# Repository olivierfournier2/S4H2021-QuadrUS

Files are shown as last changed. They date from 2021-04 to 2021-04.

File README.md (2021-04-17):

# S4H2021-QuadrUS

### Quadruped Robot | UdeS-GRO
  

## Original contributors
original_contributors <br>
**From left to right :** Anthony Breton; Jonathan Oreste Maruca; Diego-Alonso Leblanc-Romero; Charles Vuong; Mathias Bourgault; Olivier Fournier

## Final Product
gif_robot

## Table of contents
* [Development environment](#Development-environment)
    * [Needed installation](#ROS-installation)
    * [To set up this ROS project](#to-set-up-this-ROS-project)
* [Using this repository](#Using-this-repository)
    * [Creating and launching the GUI](#Creating-and-launching-the-GUI)
    * [Launching 2D and 3D simulations without GUI](#Launching-2D-and-3D-simulations-without-GUI)
* [Robot environment](#Robot-environment)

## Development environment 

### System requirements
- Ubuntu 20.04 LTS

### Dependencies
- ROS Noetic
- Gazebo
- Pybullet
- Gym
- Scipy
- Numpy
- ROS Joy
- ROS Control

### ROS installation (Development environment)
- ROS Noetic Ninjemys:  [Installation documentation](http://wiki.ros.org/noetic/Installation/Ubuntu)
- Gazebo/Rviz : Choose Desktop-Full Install option when installing ROS

### Dependencies installation (packages and second environment)
- Install Terminator

    ```
    sudo apt-get update
    ```
    ```
    sudo apt-get install terminator
    ```
- Install all dependencies for Kinematics

    ```
    sudo apt install python3-pip
    ```
    ```
    sudo apt install python-is-python3
    ```
    ```
    sudo apt install ros-noetic-joy
    ```
    ```
    sudo apt install ros-noetic-rosserial
    ```
    ```
    sudo apt install ros-noetic-rosserial-python
    ```
    ```
    sudo apt install ros-noetic-rosserial-arduino
    ```
    ```
    pip3 install pybullet
    ```
    ```
    pip3 install gym
    ```
- Install all dependencies for control
    ```
    sudo apt install ros-noetic-ros-control
    ```
    ```
    sudo apt install ros-noetic-robot-state-publisher
    ```
    ```
    sudo apt install ros-noetic-control-msgs
    ```
    
### To set up this ROS project
- Create and initialize a catkin workspace

    ```
    mkdir -p ~/quadrus_ws/src
    ```
    ```
    cd ~/quadrus_ws/src
    ```
    ```
    catkin_init_workspace
    ```

- Clone the git repository into the src folder

    ```
    git clone --recurse-submodules https://github.com/olivierfournier2/S4H2021-QuadrUS.git
    ```

- Build the ROS workspace
    ```
    cd ~/quadrus_ws
    ```

    ```
    catkin_make
    ```

    ```
    . ~/quadrus_ws/devel/setup.bash
    ```

At this point, the ROS environment should be set up and ready to work with.

## Using this repository

### Creating and launching the GUI
- Start by launching a terminal

- Access the GUI sub-folder:
    ```
    cd ~/quadrus_ws/src/S4H2021-QuadrUS/PyQt5
    ```
    
- Create the executable :
    ```
    chmod +x quadrus.py
    ```

- In this folder launch the GUI with:
    ```
    ./quadrus.py
    ```

### Launching 2D and 3D simulations without GUI
- Start by launching terminator and splitting into two terminals (T1 and T2)

- Launch roscore, the main ros node in T1:
    ```
    roscore 
    ```
    
- To view the robot model in Rviz, execute the following command in T2: 
    ```
    roslaunch qd_master qd_master.launch mode:=sim sim_mode:=kin
    ```

- To start the dynamic simulation in Gazebo, execute the following command in T2:
    ```
    roslaunch qd_master qd_master.launch mode:=sim sim_mode:=dyn
    ```

## Robot environment

### System Requirements
- RaspberryPi 4
- Ubuntu 20.04.2 LTS, 64 bit

### ROS installation
- ROS Noetic Ninjemys:  [Installation documentation](http://wiki.ros.org/noetic/Installation/Ubuntu)

### Network setup
- Set up raspberry pi as access point: [Procedure](https://gist.github.com/ExtremeGTX/ea1d1c12dde8261b263ab2fead983dc8)
- To allow ssh over wired connection, you need to set up static ip adress for both devices: [Procedure](https://linuxize.com/post/how-to-configure-static-ip-address-on-ubuntu-20-04/)

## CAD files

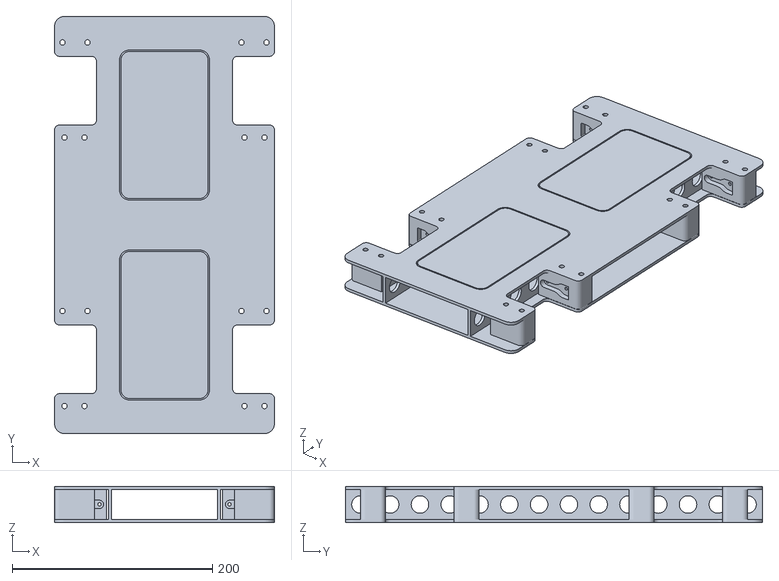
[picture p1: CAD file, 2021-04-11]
CAD/Corps/assy_corps.STL
220.0 x 417.2 x 36.4

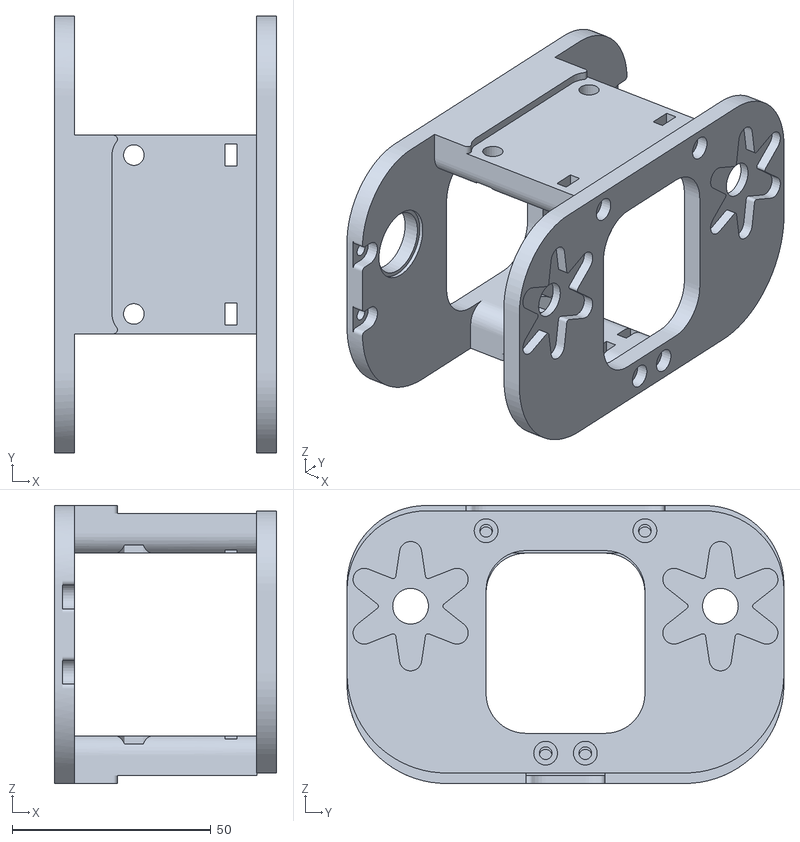
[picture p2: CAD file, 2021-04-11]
ros_packages/qd_kinematics/include/spotmini_kinematics/util/pybullet_data/assets/urdf/stl/rearmain.stl
55.9 x 110.0 x 70.0

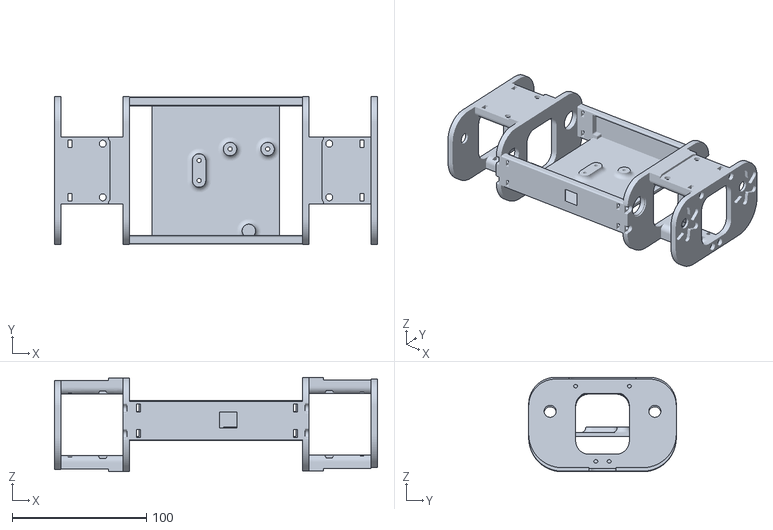
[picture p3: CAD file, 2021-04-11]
ros_packages/qd_kinematics/stl/mainbody.stl
240.7 x 110.0 x 70.4

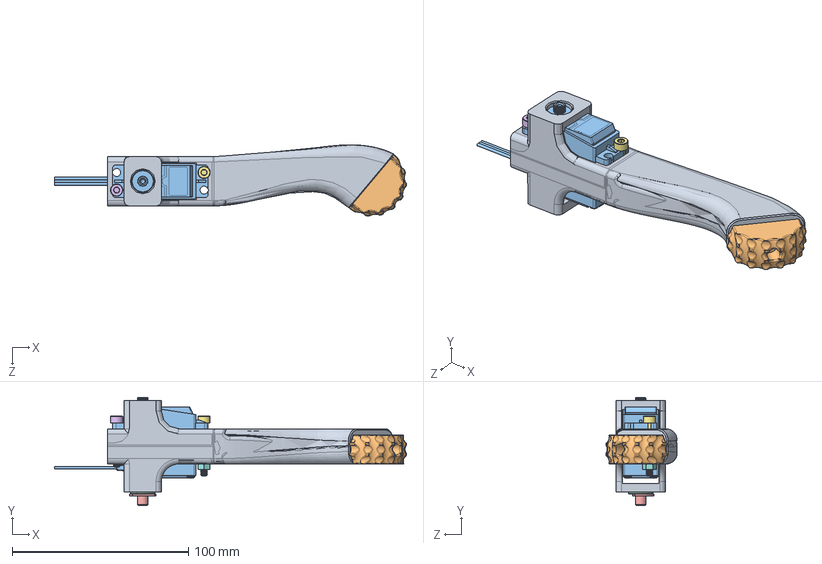
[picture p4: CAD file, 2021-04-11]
CAD/Jambe gauche/Tibia.SLDASM
199.8 x 61.4 x 40.5 mm
Tibia_V3
Embout_TPE_V3
Servo_DS3225MG
bearing_535198
Cylinde_bearing
M4x25mm
M4x30mm
M4_nut x 2

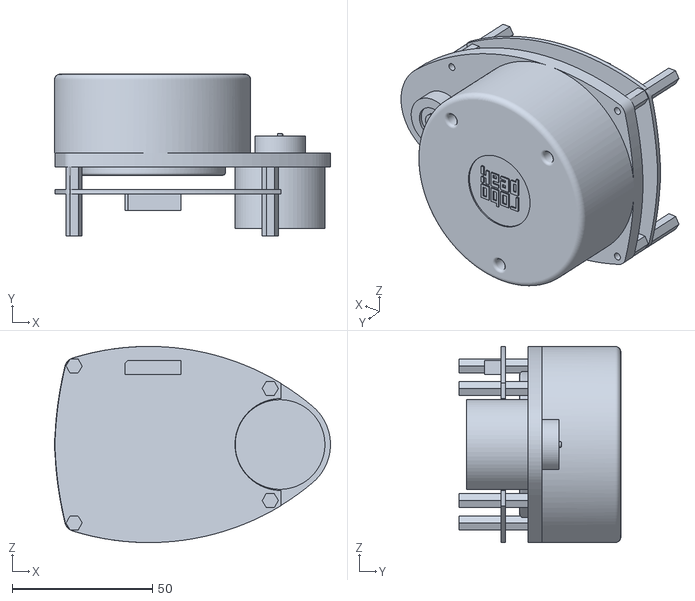
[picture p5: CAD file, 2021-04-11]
ros_packages/qd_kinematics/stl/rplidar_main.stl
98.5 x 57.7 x 70.0

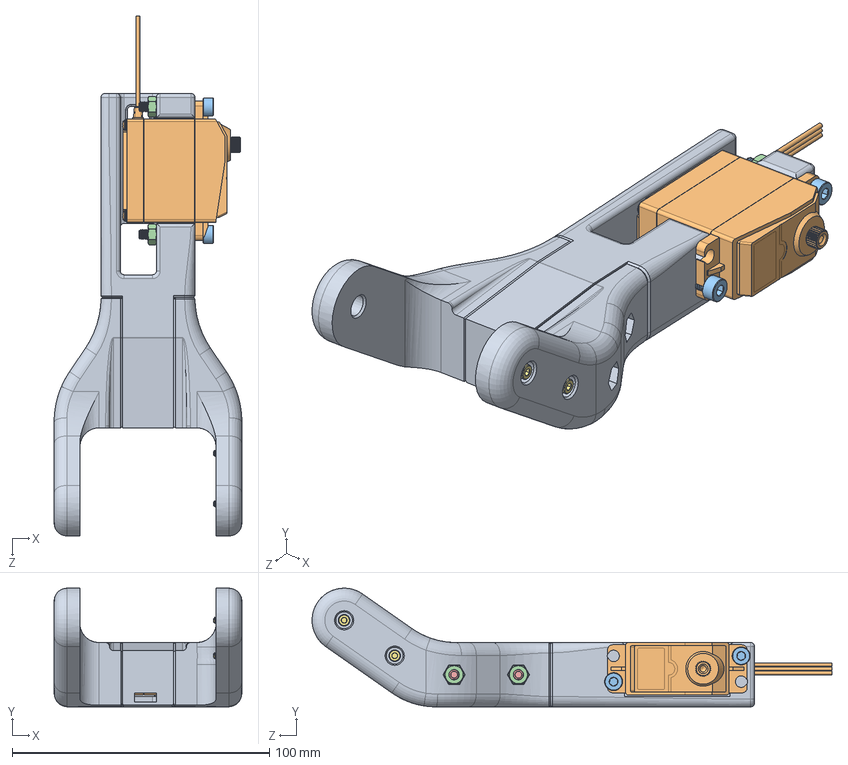
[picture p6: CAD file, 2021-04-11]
CAD/Jambe droite/Femur_D.SLDASM
73.0 x 46.2 x 202.1 mm
Femur_V3_D
Servo_DS3225MG
M4x25mm x 2
M4_nut x 4
M4x30mm x 2
Servo_helice
M2_8 x 2

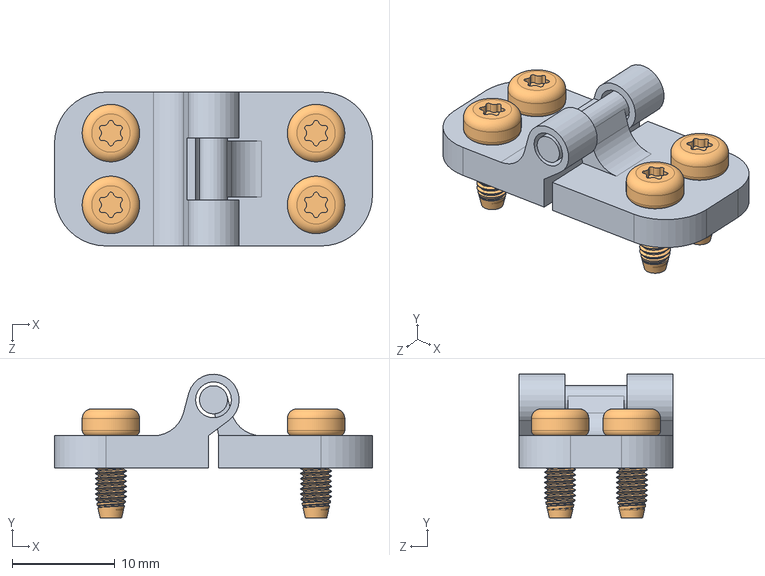
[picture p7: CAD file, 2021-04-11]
CAD/Corps/Hinge.SLDASM
31.0 x 14.0 x 15.0 mm
Hinge
M3x8mm screw x 4

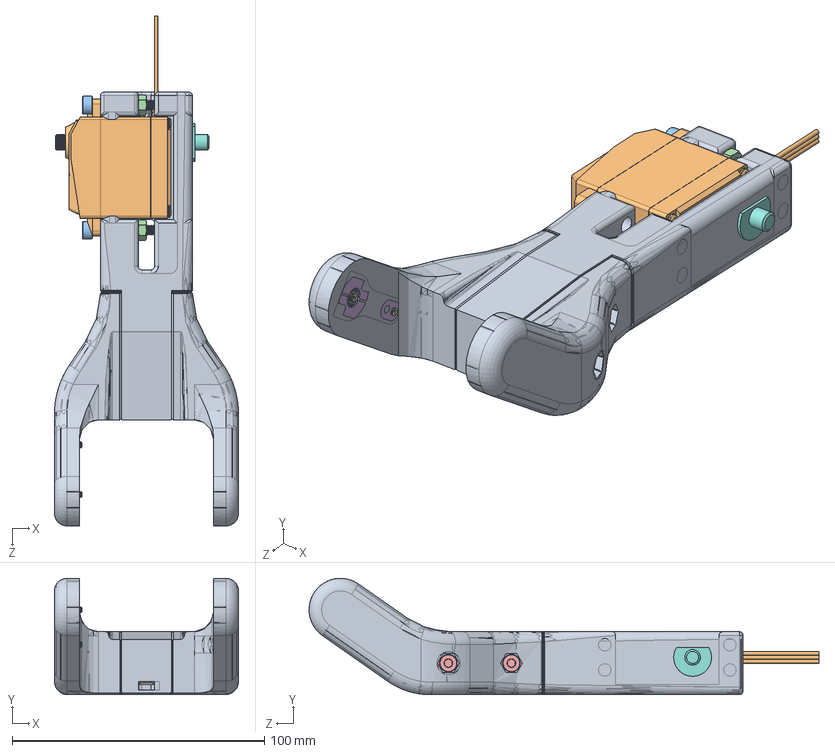
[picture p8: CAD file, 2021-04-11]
CAD/Jambe gauche/Femur.SLDASM
73.0 x 46.2 x 202.1 mm
Femur_V3
Servo_DS3225MG
M4x25mm x 2
M4_nut x 4
M4x30mm x 2
Servo_helice
M2_8 x 2
Cylinde_bearing

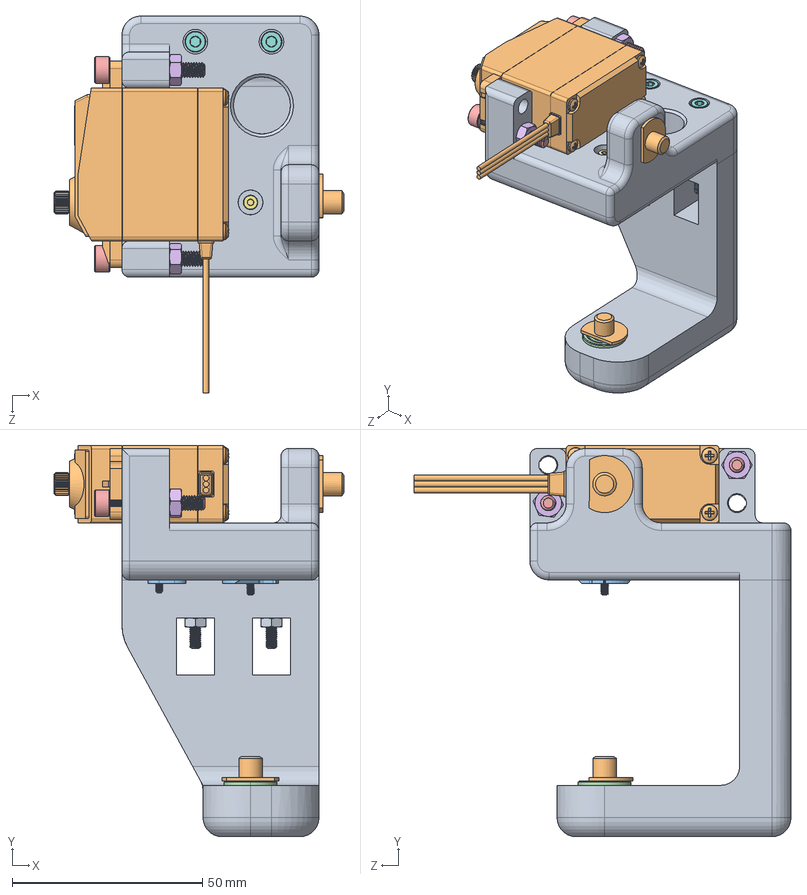
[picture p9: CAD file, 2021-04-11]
CAD/Jambe droite/Hanche_V3_D.SLDASM
76.1 x 102.9 x 99.1 mm
Hanche_V3_D2
Servo_DS3225MG
Servo_helice
bearing_535198
M4x25mm x 2
M4_nut x 2
M2x16mm x 2
M3x30mm x 2
M3_nut x 2
Cylinde_bearing x 2

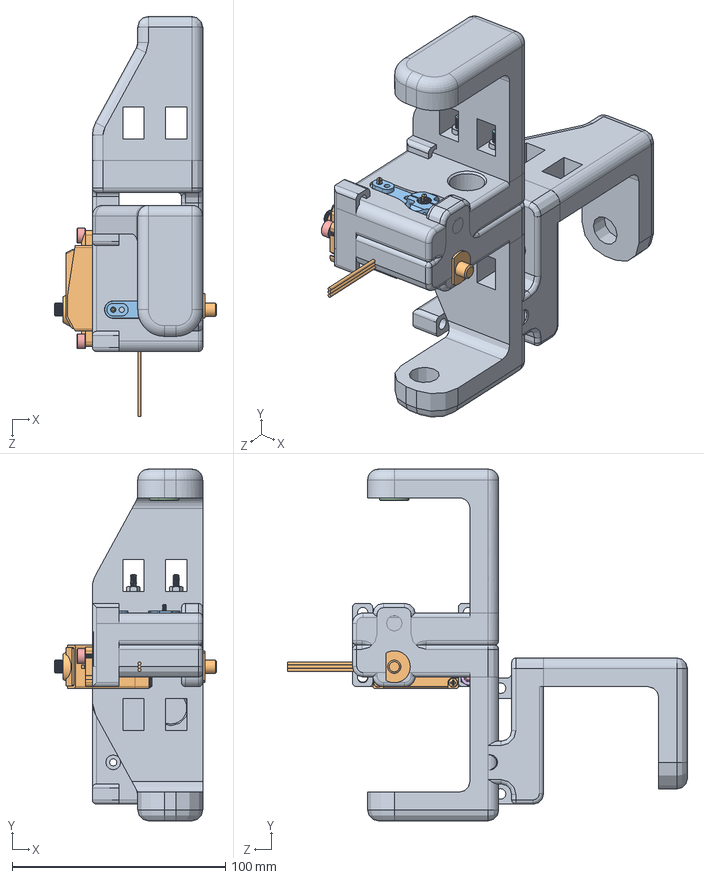
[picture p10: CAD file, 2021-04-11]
CAD/Jambe gauche/Hanche.SLDASM
76.1 x 165.0 x 187.6 mm
Hanche_V3
Servo_DS3225MG
Servo_helice
bearing_535198
M4x25mm x 2
M4_nut x 2
M2x16mm x 2
M3x30mm x 2
M3_nut x 2
Cylinde_bearing

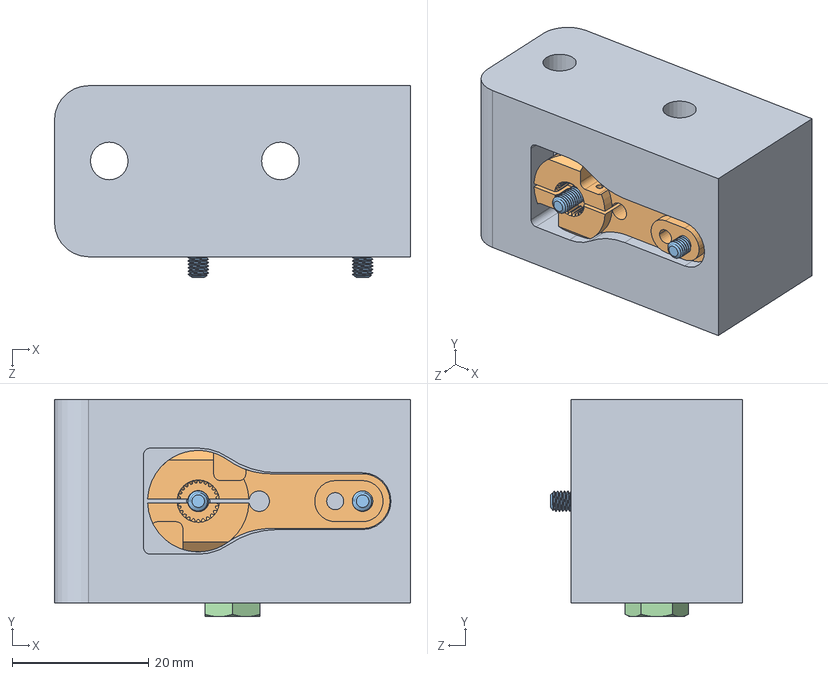
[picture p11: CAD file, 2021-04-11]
CAD/Corps/Bloc_helice.SLDASM
52.0 x 31.8 x 28.0 mm
Bloc_helice
Servo_helice
M3x20mm x 2
M5_nut x 2

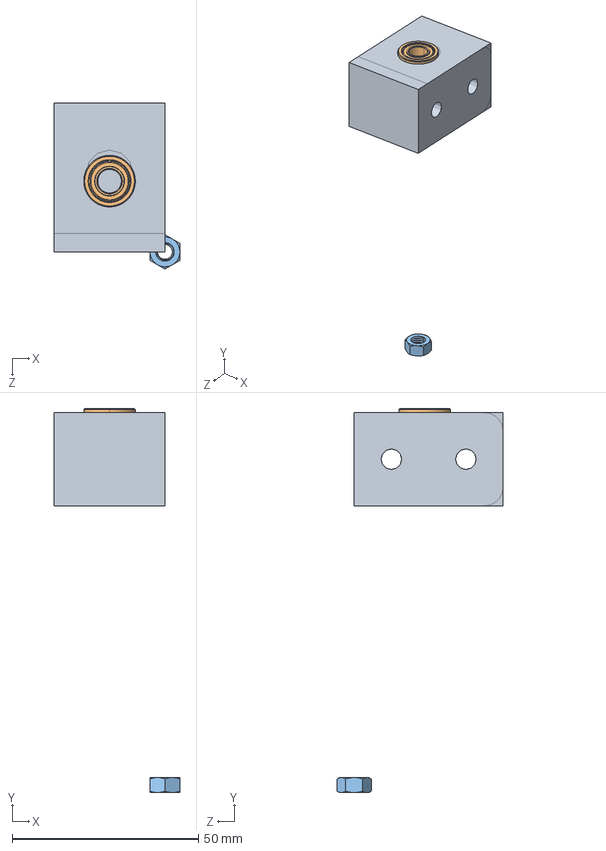
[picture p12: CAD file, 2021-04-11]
CAD/Corps/Bloc_bearing.SLDASM
33.8 x 103.1 x 44.6 mm
Bloc_bearing
bearing_535198
M5_nut x 2

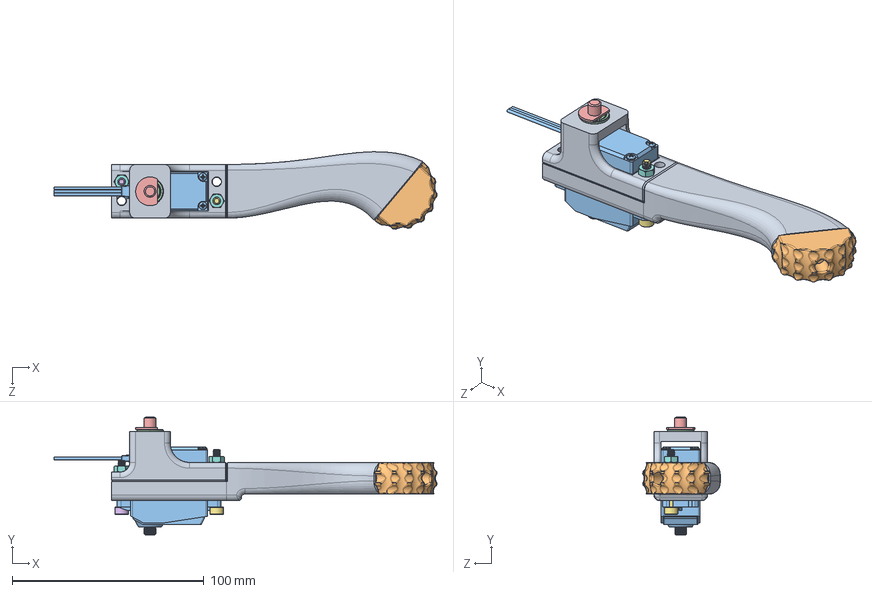
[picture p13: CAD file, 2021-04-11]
CAD/Jambe droite/Tibia_D.SLDASM
199.8 x 61.4 x 40.5 mm
Tibia_V3_D
Embout_TPE_V3
Servo_DS3225MG
bearing_535198
Cylinde_bearing
M4x25mm
M4x30mm
M4_nut x 2

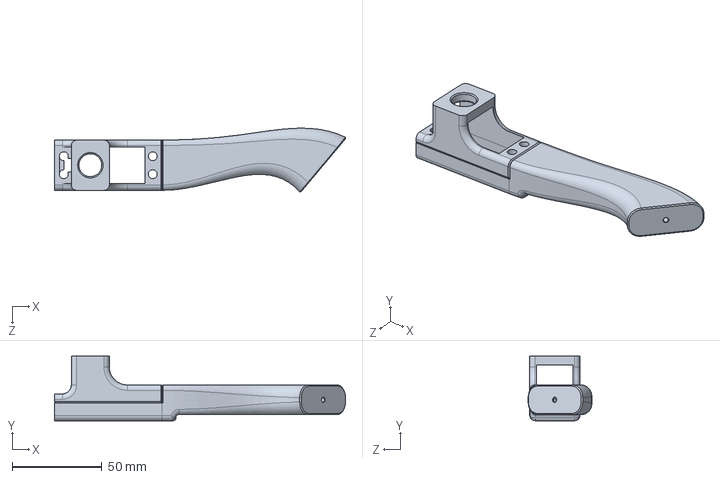
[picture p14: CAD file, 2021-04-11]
CAD/Jambe droite/Tibia_V3_D.SLDPRT
162.3 x 36.0 x 35.5 mm

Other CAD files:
CAD/Jambe gauche/Tibia_V3-Tibia_bearing.STL
CAD/Corps/Arduino-Mega.sldprt
CAD/Corps/Barre.sldprt
CAD/Corps/Bloc_bearing.STL
CAD/Corps/Bloc_bearing.sldprt
CAD/Corps/Bloc_helice.SLDPRT
CAD/Corps/Bloc_helice.STL
CAD/Corps/BottomOfBody.DXF
CAD/Corps/Drive.SLDPRT
CAD/Corps/Hinge.SLDPRT
CAD/Corps/Hinge.STL
CAD/Corps/Lock.DXF
CAD/Corps/Lock.SLDPRT
CAD/Corps/Plaque_dessous.SLDPRT
CAD/Corps/Protoboard.SLDPRT
CAD/Corps/SidesOFBody.DXF
CAD/Corps/StepDownAll.SLDPRT
CAD/Corps/StepDownPi.SLDPRT
CAD/Corps/TopOfBody.DXF
CAD/Corps/bloc_fixBearing_droite.SLDPRT
CAD/Corps/corps_bottom.SLDPRT
CAD/Jambe droite/Femur_V3_D-Stock-Femur_V3-1.STL
CAD/Jambe droite/Femur_V3_D-Stock-Femur_V3-2.STL
CAD/Jambe droite/Femur_V3_D-Stock-Femur_V3-3.STL
CAD/Jambe droite/Femur_V3_D.SLDPRT
CAD/Jambe droite/Hanche_V3_D - Cylinde_bearing-1.STL
CAD/Jambe droite/Hanche_V3_D - Cylinde_bearing-2.STL
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

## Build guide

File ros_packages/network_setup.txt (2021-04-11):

Connect to "quadrus" hotspot

Wifi IP:
192.168.4.1

Wired IP:
192.168.5.1

SSH
User: Ubuntu
Pass: Raspberry

https://husarion.com/tutorials/ros-tutorials/5-running-ros-on-multiple-machines/

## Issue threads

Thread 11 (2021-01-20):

Analyse énergétique du robot pour alimentation batterie

charlesvuong-udes, 2021-01-20:
- [ ] Dimensionner le battery pack
- [ ] Choisir le pack à acheter
- [ ] Acheter le battery pack

charlesvuong-udes, 2021-01-27:
Selon l'analyse, pour une autonomie de 30 minutes, une batterie de 6000mAh et 6V en sortie (ou plus, mais besoin d'une step-down converter) serait suffisante

AnthonyBreton, 2021-02-03:
Les moteurs on un stall current d'environ 2A. Si on peut les alimenter à 6.8V, ça serait idéal, mais sinon 6V ferait la job. À 12 moteurs qui peuvent tirer jusqu'à 2A il faut un power supply d'au moins 15A.

AnthonyBreton, 2021-02-07:
[Buck converter DC-DC input : 6V-40V / output : 1.2V-35V](https://www.amazon.ca/-/fr/dalimentation-convertisseur-Adaptateur-Constante-Convertisseur/dp/B0819Y8PJZ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)

charlesvuong-udes, 2021-02-07:
- Une analyse a été faite pour l'alimentation filaire. On pourrait acheter un power supply (style power supply d'imprimante 3D) qui fourni 12V et a un courant max de 20A.

- L'option de power supply (style chargeur d'ordinateur portable) n'offre pas beaucoup de choix si on veut fournir jusqu'à 20A. Il y en a de 12V et 10A.

- Dans tous les cas, il est fort probable qu'il va falloir s'acheter un [step-down converter](https://www.amazon.ca/-/fr/dalimentation-convertisseur-Adaptateur-Constante-Convertisseur/dp/B0819Y8PJZ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) pour réduire la tension en entrée des moteurs, car il n'y a pas de power supply qui fourni 6.8V à 20A max.

- Lorsqu'on aura une meilleure idée de la consommation de courant des 12 moteurs en fonctionnement normal, on pourra dimensionner une batterie en conséquence.

Closed 2021-03-24.

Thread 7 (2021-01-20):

Sélection des moteurs

charlesvuong-udes, 2021-01-20:
- [x] Dimensionnement des moteurs
- [x] Choix des moteurs
- [ ] Achats des moteurs

Recherche sur les différentes possibilités

AnthonyBreton, 2021-01-20:
#### Moteur Dynamixel AX-12A pack de 6
https://emanual.robotis.com/docs/en/dxl/ax/ax-12a/ -> specsheet
- 224,50$ USD -> 309,25$ CAD
- Stall Torque 1,5 N*m
#### Moteur Dynamixel XL430-W250-T **2 prêté par l'uni**
https://www.robotis.us/dynamixel-xl430-w250-t/ -> specsheet
- Stall Torque 1,5 N*m donc le même que pour les AX-12A
On pourrait prendre 8 moteurs pour faire le robot et donc avoir seulement le pack de 6 à acheter. Voir l'image pour 2 moteurs par pattes. (Aucun moteur au niveau du genous, rotation faite par transmission de mouvement)
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

AnthonyBreton, 2021-01-20:
Voir le document word sur team **Choix des moteurs** path -> Général/Documentation

charlesvuong-udes, 2021-01-26:
Lien vers le paquet de 4 moteurs
https://www.amazon.ca/-/fr/servomoteurs-num%C3%A9riques-%C3%A9tanches-DS3225-servomoteur/dp/B088GV6VND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

AnthonyBreton, 2021-01-27:
Library Arduino pour contrôler les servos https://www.arduino.cc/reference/en/libraries/servo/

Closed 2021-03-24.

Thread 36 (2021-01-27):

Contrôle des moteurs

AnthonyBreton, 2021-01-27:

AnthonyBreton, 2021-01-27:
- Bonne vidéo pour contrôler plusieurs moteurs : [16 servos](https://www.youtube.com/watch?v=LXURLvga8bQ&ab_channel=HowToMechatronics)
- Board qui permet le contrôle de 16 moteurs : PCA9685

AnthonyBreton, 2021-02-03:
[Adafruit PCA9685 Guide](https://learn.adafruit.com/16-channel-pwm-servo-driver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)
[Library Adafruit PCA9685](https://github.com/adafruit/Adafruit-PWM-Servo-Driver-Library) aussi installable à partir de Arduino IDE library manager

AnthonyBreton, 2021-02-24:
### Algorithme de contrôle open CR C++ ###
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

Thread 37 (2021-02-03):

Corrections du CAD

AnthonyBreton, 2021-02-03:

Closed 2021-03-24.

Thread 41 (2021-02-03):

Caractériser les moteurs (couples, courant, voltage) avec banc de test

AnthonyBreton, 2021-02-03:

charlesvuong-udes, 2021-02-07:
L'essai à 6.8V est anormale à partir de 2A. Si on choisi d'utiliser 6.8V comme tension d'alimentation, il serait bien de refaire les essais pour corriger les données.

AnthonyBreton, 2021-02-07:
Le max qu'on peut aller avec le PCA9685 c'est 6V par contre, donc ça ne devrait pas être trop grave et ça donne déjà une bonne idée

AnthonyBreton, 2021-02-24:
### Essais statiques  ###

- Fmax: 16.5 N à 6.8 V

- Bras de levier: 125 mm

- Couple moteur: 2.07 Nm
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
### Essais dynamiques  ###

- 750 grammes

- Bras de levier: 125 mm

- 0.5 tour/s
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

** Voir teams General/Documentation/Choix moteurs/Couple moteur/Banc de test couple_avec graphique.xlsx pour les données de tests**

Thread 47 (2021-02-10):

Développement de la cinématique inverse ROS

mathiasbourgault, 2021-02-10:
Kdl package
ou
Python

mathiasbourgault, 2021-02-10:
tuto implementation IK + moveit: https://www.youtube.com/watch?v=G-XXnPHYhxs

mathiasbourgault, 2021-02-12:
Moveit download
Moveit setup assistant tuto: http://docs.ros.org/en/kinetic/api/moveit_tutorials/html/doc/setup_assistant/setup_assistant_tutorial.html

Closed 2021-03-24.

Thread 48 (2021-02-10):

Creation du node pour le joystick

marj3220, 2021-02-10:
Lire les inputs du joystick
Publish ce qui est necessaire pour le control

LIRE DOCUMENTATION de ROS joy

Probabilite dun deuxieme node qui traite les inputs selon une curve pour les accelerations

Closed 2021-03-24.

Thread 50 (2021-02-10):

Produits à acheter

charlesvuong-udes, 2021-02-10:
- Power supply
- Moteurs
- Step-down converter

charlesvuong-udes, 2021-02-15:
- Power supply: Certification CE, correct pour utilisation à l'université

- Step-down: Efficacité de conversion, 96%. Devrait être le bon modèle qui transforme la tension de trop en courant. Il va falloir surveiller la température de cette composante lorsqu'on va dépasser 10A. S'il chauffe trop, on peut ajouter une petite fan pour créer un déplacement d'air prêt du heat sink

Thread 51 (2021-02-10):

Programmation contrôle

charlesvuong-udes, 2021-02-10:
- Regarder librairie du driver PCA9685
- Regarder rosserial pour la communication
- Regarder multi-threading pour pouvoir faire plusieurs actions en même temps

Closed 2021-03-24.

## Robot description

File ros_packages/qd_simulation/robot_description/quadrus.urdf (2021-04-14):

<?xml version="1.0" ?>
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
<robot name="quadrus">
  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
  <link name="base_link"/>
  <joint name="floating" type="fixed">
    <parent link="base_link"/>
    <child link="chassis"/>
    <origin xyz="0 0 0"/>
  </joint>
  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
  <link name="chassis">
    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
    <inertial>
      <mass value="0.97859"/>
      <origin xyz="-0.01428 0.00536 -0.00018"/>
      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
    </inertial>
  </link>
  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
  <link name="link_front_left_hip">
    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
    <inertial>
      <mass value="0.1191"/>
      <origin xyz="0.00364 0.0025 0.01974"/>
      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
    </inertial>
  </link>
  <joint name="J1" type="revolute">
    <parent link="chassis"/>
    <child link="link_front_left_hip"/>
    <origin rpy="0 0 0" xyz="0.12 0.089 0"/>
    <limit effort="30" lower="-0.401" upper="0.785" velocity="10"/>
    <axis xyz="1 0 0"/>
  </joint>
  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
  <link name="link_front_left_upperleg">
    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
    <inertial>
      <mass value="0.13118"/>
      <origin xyz="-0.041697 -0.007043 -0.000214"/>
      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
    </inertial>
  </link>
  <joint name="J2" type="revolute">
    <parent link="link_front_left_hip"/>
    <child link="link_front_left_upperleg"/>
    <origin rpy="0 0 0" xyz="0 0.05925 0"/>
    <limit effort="30" lower="-1.5" upper="0.7" velocity="10"/>
    <axis xyz="0 1 0"/>
  </joint>
  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
  <link name="link_front_left_lowerleg">
    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
    <inertial>
      <mass value="0.10059"/>
      <origin xyz=" 0.025048 -0.002594 0.000523"/>
      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
    </inertial>
  </link>
  <joint name="J3" type="revolute">
    <parent link="link_front_left_upperleg"/>
    <child link="link_front_left_lowerleg"/>
    <origin rpy="0 1.5708 0" xyz="-0.1396 0 -0.01886"/>
    <axis xyz="0 1 0"/>
    <limit effort="30" lower="-1.396" upper="1.745" velocity="10"/>
  </joint>
  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
  <link name="link_front_left_paw">
    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
    <inertial>
      <mass value="0.003"/>
      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
    </inertial>
  </link>
  <joint name="joint_front_left_paw" type="fixed">
    <parent link="link_front_left_lowerleg"/>
    <child link="link_front_left_paw"/>
    <origin rpy="0 0.698 0" xyz="0.1296 0 0"/>
  </joint>
  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
  <link name="link_front_right_hip">
    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
    <inertial>
      <mass value="0.1191"/>
      <origin xyz="0.00364 0.0025 0.01974"/>
      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
    </inertial>
  </link>
  <joint name="J4" type="revolute">
    <parent link="chassis"/>
    <child link="link_front_right_hip"/>
    <origin rpy="0 0 0" xyz="0.12 -0.089 0"/>
    <limit effort="30" lower="-0.785" upper="0.401" velocity="10"/>
    <axis xyz="1 0 0"/>
  </joint>
  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
  <link name="link_front_right_upperleg">
    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
    <inertial>
      <mass value="0.13118"/>
      <origin xyz="-0.041697 -0.007043 -0.000214"/>
      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
    </inertial>
  </link>
  <joint name="J5" type="revolute">
    <parent link="link_front_right_hip"/>
    <child link="link_front_right_upperleg"/>
    <origin rpy="0 0 0" xyz="0 -0.05925 0"/>
    <limit effort="1" lower="-1.5" upper="0.7" velocity="1.0"/>
    <axis xyz="0 1 0"/>
  </joint>
  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
  <link name="link_front_right_lowerleg">
    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
    <inertial>
      <mass value="0.10059"/>
      <origin xyz=" 0.025048 -0.002594 0.000523"/>
      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
    </inertial>
  </link>
  <joint name="J6" type="revolute">
    <parent link="link_front_right_upperleg"/>
    <child link="link_front_right_lowerleg"/>
    <origin rpy="0 1.5708 0" xyz="-0.1396 0 -0.01886"/>
    <axis xyz="0 1 0"/>
    <limit effort="30" lower="-1.745" upper="1.396" velocity="10"/>
  </joint>
  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
  <link name="link_front_right_paw">
    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
    <inertial>
      <mass value="0.003"/>
      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
    </inertial>
  </link>
  <joint name="joint_front_right_paw" type="fixed">
    <parent link="link_front_right_lowerleg"/>
    <child link="link_front_right_paw"/>
    <origin rpy="0 0.698 0" xyz="0.1296 0 0"/>
  </joint>
  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
  <link name="link_back_left_hip">
    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
    <inertial>
      <mass value="0.1191"/>
      <origin xyz="0.00364 0.0025 0.01974"/>
      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
    </inertial>
  </link>
  <joint name="J7" type="revolute">
    <parent link="chassis"/>
    <child link="link_back_left_hip"/>
    <origin rpy="0 0 0" xyz="-0.1486 0.089 0"/>
    <limit effort="30" lower="-0.401" upper="0.785" velocity="10"/>
    <axis xyz="1 0 0"/>
  </joint>
  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
  <link name="link_back_left_upperleg">
    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
    <inertial>
      <mass value="0.13118"/>
      <origin xyz="-0.041697 -0.007043 -0.000214"/>
      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
    </inertial>
  </link>
  <joint name="J8" type="revolute">
    <parent link="link_back_left_hip"/>
    <child link="link_back_left_upperleg"/>
    <origin rpy="0 0 0" xyz="0 0.05925 0"/>
    <limit effort="30" lower="-1.5" upper="0.7" velocity="10"/>
    <axis xyz="0 1 0"/>
  </joint>
  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
  <link name="link_back_left_lowerleg">
    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
    <inertial>
      <mass value="0.10059"/>
      <origin xyz=" 0.025048 -0.002594 0.000523"/>
      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
    </inertial>
  </link>
  <joint name="J9" type="revolute">
    <parent link="link_back_left_upperleg"/>
    <child link="link_back_left_lowerleg"/>
    <origin rpy="0 1.5708 0" xyz="-0.1396 0 -0.01886"/>
    <axis xyz="0 1 0"/>
    <limit effort="30" lower="-1.396" upper="1.745" velocity="10"/>
  </joint>
  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
  <link name="link_back_left_paw">
    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
    <inertial>
      <mass value="0.003"/>
      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
    </inertial>
  </link>
  <joint name="joint_back_left_paw" type="fixed">
    <parent link="link_back_left_lowerleg"/>
    <child link="link_back_left_paw"/>
    <origin rpy="0 0.698 0" xyz="0.1296 0 0"/>
  </joint>
  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
  <link name="link_back_right_hip">
    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
    <inertial>
      <mass value="0.1191"/>
      <origin xyz="0.00364 0.0025 0.01974"/>
      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
    </inertial>
  </link>
  <joint name="J10" type="revolute">
    <parent link="chassis"/>
    <child link="link_back_right_hip"/>
    <origin rpy="0 0 0" xyz="-0.1486 -0.089 0"/>
    <limit effort="30" lower="-0.785" upper="0.401" velocity="10"/>
    <axis xyz="1 0 0"/>
  </joint>
  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
  <link name="link_back_right_upperleg">
    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
    <inertial>
      <mass value="0.13118"/>
      <origin xyz="-0.041697 -0.007043 -0.000214"/>
      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
    </inertial>
  </link>
  <joint name="J11" type="revolute">
    <parent link="link_back_right_hip"/>
    <child link="link_back_right_upperleg"/>
    <origin rpy="0 0 0" xyz="0 -0.05925 0"/>
    <limit effort="1" lower="-1.5" upper="0.7" velocity="1.0"/>
    <axis xyz="0 1 0"/>
  </joint>
  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
  <link name="link_back_right_lowerleg">
    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
    <inertial>
      <mass value="0.10059"/>
      <origin xyz=" 0.025048 -0.002594 0.000523"/>
      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
    </inertial>
  </link>
  <joint name="J12" type="revolute">
    <parent link="link_back_right_upperleg"/>
    <child link="link_back_right_lowerleg"/>
    <origin rpy="0 1.5708 0" xyz="-0.1396 0 -0.01886"/>
    <axis xyz="0 1 0"/>
    <limit effort="30" lower="-1.745" upper="1.396" velocity="10"/>
  </joint>
  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
  <link name="link_back_right_paw">
    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
    <inertial>
      <mass value="0.003"/>
      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
    </inertial>
  </link>
  <joint name="joint_back_right_paw" type="fixed">
    <parent link="link_back_right_lowerleg"/>
    <child link="link_back_right_paw"/>
    <origin rpy="0 0.698 0" xyz="0.1296 0 0"/>
  </joint>
  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
</robot>

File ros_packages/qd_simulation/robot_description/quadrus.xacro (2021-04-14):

<?xml version='1.0'?>
<robot name="quadrus" xmlns:xacro="http://www.ros.org/wiki/xacro">

	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
	<xacro:property name="PI" value="3.1415926535897931"/>
	
	<xacro:property name="hip_offset" value="0.05925" /> 
	<xacro:property name="upperleg_length" value="0.1396" /> 
	<xacro:property name="upperleg_offset" value="0.01886" /> 
	<xacro:property name="lowerleg_length" value="0.1296" />

	<xacro:property name="rear_hip_long_offset" value="-0.1486" /> 
	<xacro:property name="hip_long_center_dist" value="0.2686" />
	<xacro:property name="hip_lat_center_dist" value="0.178" />
	
	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
	<xacro:include filename="$(find qd_simulation)/robot_description/materials.xacro" />
	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
	<xacro:include filename="$(find qd_simulation)/robot_description/quadrus.gazebo" />

	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
	<link name="base_link"/>

	<joint name="floating" type="fixed">
		<parent link="base_link"/>
		<child link="chassis"/>
		<origin xyz="0 0 0"/>
	</joint>

	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
		<link name="chassis">
			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
		
			<inertial>
				<mass value="0.97859"/>
				<origin xyz="-0.01428 0.00536 -0.00018"/>
				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
			</inertial>	

		</link>
			
		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

	<xacro:macro name="quadrus_leg" params="long lat id">
		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
			<xacro:property name="hip_joint_id" value="J${(id-1)*3+1}"/>

			<link name="link_${long}_${lat}_hip">
				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

				<inertial>
					<mass value="0.1191"/>
					<origin xyz="0.00364 0.0025 0.01974"/>
					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
				</inertial>	

			</link>

			<joint name="${hip_joint_id}" type="revolute">
				<parent link="chassis"/>
				<child link="link_${long}_${lat}_hip"/>

				<xacro:if value="${long == 'front' and lat == 'left'}">
					<origin xyz="${rear_hip_long_offset+hip_long_center_dist} ${hip_lat_center_dist/2.0} 0" rpy="0 0 0" />
					<limit effort="30" velocity="10" lower="-0.401" upper="0.785" />
				</xacro:if>

				<xacro:if value="${long == 'front' and lat == 'right'}">
					<origin xyz="${rear_hip_long_offset+hip_long_center_dist} ${-hip_lat_center_dist/2.0} 0" rpy="0 0 0" /> 
					<limit effort="30" velocity="10" lower="-0.785" upper="0.401" />
				</xacro:if>

				<xacro:if value="${long == 'back' and lat == 'left'}">
					<origin xyz="${rear_hip_long_offset} ${hip_lat_center_dist/2.0} 0" rpy="0 0 0" /> 
					<limit effort="30" velocity="10" lower="-0.401" upper="0.785" />
				</xacro:if>

				<xacro:if value="${long == 'back' and lat == 'right'}">
					<origin xyz="${rear_hip_long_offset} ${-hip_lat_center_dist/2.0} 0" rpy="0 0 0" /> 
					<limit effort="30" velocity="10" lower="-0.785" upper="0.401" />
				</xacro:if>

				<axis xyz="1 0 0" />
				
			</joint>

			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
			<xacro:property name="upperleg_joint_id" value="J${(id-1)*3+2}"/>

			<link name="link_${long}_${lat}_upperleg">
				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

				<inertial>
					<mass value="0.13118"/>
					<origin xyz="-0.041697 -0.007043 -0.000214"/>
					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
				</inertial>

			</link>

			<joint name="${upperleg_joint_id}" type="revolute">
				<parent link="link_${long}_${lat}_hip"/>
				<child link="link_${long}_${lat}_upperleg"/>

				<xacro:if value="${lat == 'left'}">
					<origin xyz="0 ${hip_offset} 0" rpy="0 0 0" />
					<limit effort="30" velocity="10" lower="-1.5" upper="0.7" />
				</xacro:if>

				<xacro:if value="${lat == 'right'}">
					<origin xyz="0 ${-hip_offset} 0" rpy="0 0 0" />
					<limit effort="1" velocity="1.0" lower="-1.5" upper="0.7" />
				</xacro:if>

				<axis xyz="0 1 0" />

			</joint>

			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	
			<xacro:property name="lowerleg_joint_id" value="J${(id-1)*3+3}"/>

			<link name="link_${long}_${lat}_lowerleg">
				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

				<inertial>
					<mass value="0.10059"/>
					<origin xyz=" 0.025048 -0.002594 0.000523"/>
					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
				</inertial>

			</link>

			<joint name="${lowerleg_joint_id}" type="revolute">
				<parent link="link_${long}_${lat}_upperleg"/>
				<child link="link_${long}_${lat}_lowerleg"/>
				<origin xyz="${-upperleg_length} 0 ${-upperleg_offset}" rpy="0 1.5708 0" /> 
				<axis xyz="0 1 0" />

				<xacro:if value="${lat == 'right'}">
					<limit effort="30" velocity="10" lower="-1.745" upper="1.396" />
				</xacro:if>

				<xacro:if value="${lat == 'left'}">
					<limit effort="30" velocity="10" lower="-1.396" upper="1.745" />
				</xacro:if>

			</joint>

			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	
			<link name="link_${long}_${lat}_paw">
				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

				<inertial>
					<mass value="0.003"/>
					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
				</inertial>

			</link>

			<joint name="joint_${long}_${lat}_paw" type="fixed">
				<parent link="link_${long}_${lat}_lowerleg"/>
				<child link="link_${long}_${lat}_paw"/>
				<origin xyz="${lowerleg_length} 0 0" rpy="0 0.698 0" /> 
			</joint>

			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
	
	</xacro:macro>

	<xacro:quadrus_leg long="front" lat="left" id="1"/>
	<xacro:quadrus_leg long="front" lat="right" id="2"/>
	<xacro:quadrus_leg long="back" lat="left" id="3"/>
	<xacro:quadrus_leg long="back" lat="right" id="4"/>
	
</robot>

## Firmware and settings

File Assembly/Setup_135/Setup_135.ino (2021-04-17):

/* Sweep
 by BARRAGAN <http://barraganstudio.com>
 This example code is in the public domain.

 modified 8 Nov 2013
 by Scott Fitzgerald
 http://www.arduino.cc/en/Tutorial/Sweep
*/
#include <Adafruit_PWMServoDriver.h>

Adafruit_PWMServoDriver driver = Adafruit_PWMServoDriver();;

int pos = 0;    // variable to store the servo position
const int pulsemin = 555;
const int pulsemax[12] = {2395, 2400, 2410,
                          2350, 2410, 2425,
                          2417, 2405, 2415,
                          2415, 2410, 2425};

int degToPulse(float ang, int motorIndex) {
  if (motorIndex == 3)
  {
    return ang*(pulsemax[motorIndex]-pulsemin)/180.0 + pulsemin;
  } else {
    return ang*(pulsemax[motorIndex]-pulsemin)/270.0 + pulsemin;
  }
}

void setup() {
  driver.begin();
  driver.setOscillatorFrequency(27000000);
  driver.setPWMFreq(60);
}

void loop() {

  driver.writeMicroseconds(0,degToPulse(135,0));
  //delay(1000);
}

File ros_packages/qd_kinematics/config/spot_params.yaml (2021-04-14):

# MEASURE
# COM to Shoulder
shoulder_length: 0.089 #0.05925 (plan milieu femur - axe rot hanche)
# Shoulder to Elbow
elbow_length: 0.1408
# Elbow to Wrist
wrist_length: 0.1296
# Forward Hip Separation
hip_x: 0.2683
# Lateral Hip Separation
hip_y: 0.178

# ADJUSTABLE
# Stance Length
foot_x: 0.268
# Stance Width
foot_y: 0.34
# Stance Height
height: 0.2
# Adjust for balanced walk
com_offset: -0.05

# Time Step
dt: 0.001

# Swing Period (lower is faster)
Tswing: 0.4
SwingPeriod_LIMITS: [0.1, 0.4]

# Step Velocity (Using very low value as my main form of speed control is swing period)
BaseStepVelocity: 0.001

# Foot Clearance Height
BaseClearanceHeight: 0.015
ClearanceHeight_LIMITS: [0.0, 0.04]

# Foot Penetration Depth
BasePenetrationDepth: 0.002
PenetrationDepth_LIMITS: [0.0, 0.02]

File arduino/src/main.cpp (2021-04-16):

#include "qd_hw_control.h"
#include "qd_hw_config.h"

Adafruit_PWMServoDriver driver = Adafruit_PWMServoDriver();
ros::NodeHandle nh;
std_msgs::Float64MultiArray cmd_msg;
std_msgs::Int16 test_int;
std_msgs::Float64MultiArray feedback_msg;

ros::Publisher feedback_pub(feedback_topic, &feedback_msg);
ros::Subscriber<std_msgs::Float64MultiArray> cmd_sub(cmd_topic,
                                                     &subscriberCallback);

void setup() {
  servoInit();
  computeLimits();
  moveMotor(initPositions);
  rosInit();
}

void loop() {

  if(feedback_state){ 
    readAngles(&feedback_msg);
    feedback_pub.publish(&feedback_msg);
  }

  nh.spinOnce();
  delay(1000.0/loop_hz);
}

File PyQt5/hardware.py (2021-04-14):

# -*- coding: utf-8 -*-

# Form implementation generated from reading ui file 'hardware.ui'
#
# Created by: PyQt5 UI code generator 5.14.1
#
# WARNING! All changes made in this file will be lost!


from PyQt5 import QtCore, QtGui, QtWidgets
import os
import time
import sys
from random import randint
import rospkg
rospack = rospkg.RosPack()


class Ui_hardwareWindow(object):
    def setupUi(self, hardwareWindow):
        hardwareWindow.setObjectName("hardwareWindow")
        hardwareWindow.resize(947, 744)
        hardwareWindow.setStyleSheet("background-color: rgb(238, 238, 236);")
        self.centralwidget = QtWidgets.QWidget(hardwareWindow)
        self.centralwidget.setObjectName("centralwidget")
        self.EstopButton = QtWidgets.QPushButton(self.centralwidget)
        self.EstopButton.setGeometry(QtCore.QRect(40, 370, 231, 101))
        self.EstopButton.setStyleSheet("background-color: rgb(245, 121, 0);\n"
"font: 75 oblique 15pt \"Ubuntu Condensed\";")
        self.EstopButton.setObjectName("EstopButton")
        self.label = QtWidgets.QLabel(self.centralwidget)
        self.label.setGeometry(QtCore.QRect(0, 0, 231, 131))
        font = QtGui.QFont()
        font.setFamily("Ubuntu Condensed")
        font.setPointSize(30)
        font.setBold(True)
        font.setItalic(True)
        font.setWeight(75)
        self.label.setFont(font)
        self.label.setLayoutDirection(QtCore.Qt.LeftToRight)
        self.label.setAutoFillBackground(False)
        self.label.setStyleSheet("color: rgb(78, 154, 6);\n"
"")
        self.label.setAlignment(QtCore.Qt.AlignCenter)
        self.label.setWordWrap(False)
        self.label.setObjectName("label")
        self.enableButton = QtWidgets.QPushButton(self.centralwidget)
        self.enableButton.setGeometry(QtCore.QRect(40, 170, 231, 101))
        self.enableButton.setStyleSheet("background-color: rgb(252, 233, 79);\n"
"font: 75 oblique 15pt \"Ubuntu Condensed\";")
        self.enableButton.setObjectName("enableButton")
        self.backButton = QtWidgets.QPushButton(self.centralwidget)
        self.backButton.setGeometry(QtCore.QRect(20, 600, 201, 71))
        self.backButton.setStyleSheet("background-color: rgb(186, 189, 182);\n"
"font: 75 oblique 15pt \"Ubuntu Condensed\";")
        self.backButton.setObjectName("backButton")
        self.M1_command = QtWidgets.QLCDNumber(self.centralwidget)
        self.M1_command.setGeometry(QtCore.QRect(610, 80, 64, 23))
        self.M1_command.setObjectName("M1_command")
        self.M1_command.setStyleSheet("background-color: rgb(0, 0, 0);")
        self.M2_command = QtWidgets.QLCDNumber(self.centralwidget)
        self.M2_command.setGeometry(QtCore.QRect(610, 120, 64, 23))
        self.M2_command.setObjectName("M2_command")
        self.M2_command.setStyleSheet("background-color: rgb(0, 0, 0);")
        self.M3_command = QtWidgets.QLCDNumber(self.centralwidget)
        self.M3_command.setGeometry(QtCore.QRect(610, 160, 64, 23))
        self.M3_command.setObjectName("M3_command")
        self.M3_command.setStyleSheet("background-color: rgb(0, 0, 0);")
        self.M4_command = QtWidgets.QLCDNumber(self.centralwidget)
        self.M4_command.setGeometry(QtCore.QRect(610, 220, 64, 23))
        self.M4_command.setObjectName("M4_command")
        self.M4_command.setStyleSheet("background-color: rgb(0, 0, 0);")
        self.M5_command = QtWidgets.QLCDNumber(self.centralwidget)
        self.M5_command.setGeometry(QtCore.QRect(610, 260, 64, 23))
        self.M5_command.setObjectName("M5_command")
        self.M5_command.setStyleSheet("background-color: rgb(0, 0, 0);")
        self.M6_command = QtWidgets.QLCDNumber(self.centralwidget)
        self.M6_command.setGeometry(QtCore.QRect(610, 300, 64, 23))
        self.M6_command.setObjectName("M6_command")
        self.M6_command.setStyleSheet("background-color: rgb(0, 0, 0);")
        self.M7_command = QtWidgets.QLCDNumber(self.centralwidget)
        self.M7_command.setGeometry(QtCore.QRect(610, 360, 64, 23))
        self.M7_command.setObjectName("M7_command")
        self.M7_command.setStyleSheet("background-color: rgb(0, 0, 0);")
        self.M8_command = QtWidgets.QLCDNumber(self.centralwidget)
        self.M8_command.setGeometry(QtCore.QRect(610, 400, 64, 23))
        self.M8_command.setObjectName("M8_command")
        self.M8_command.setStyleSheet("background-color: rgb(0, 0, 0);")
        self.M9_command = QtWidgets.QLCDNumber(self.centralwidget)
        self.M9_command.setGeometry(QtCore.QRect(610, 440, 64, 23))
        self.M9_command.setObjectName("M9_command")
        self.M9_command.setStyleSheet("background-color: rgb(0, 0, 0);")
        self.M10_command = QtWidgets.QLCDNumber(self.centralwidget)
        self.M10_command.setGeometry(QtCore.QRect(610, 500, 64, 23))
        self.M10_command.setObjectName("M10_command")
        self.M10_command.setStyleSheet("background-color: rgb(0, 0, 0);")
        self.M12_command = QtWidgets.QLCDNumber(self.centralwidget)
        self.M12_command.setGeometry(QtCore.QRect(610, 580, 64, 23))
        self.M12_command.setObjectName("M12_command")
        self.M12_command.setStyleSheet("background-color: rgb(0, 0, 0);")
        self.M11_command = QtWidgets.QLCDNumber(self.centralwidget)
        self.M11_command.setGeometry(QtCore.QRect(610, 540, 64, 23))
        self.M11_command.setObjectName("M11_command")
        self.M11_command.setStyleSheet("background-color: rgb(0, 0, 0);")
        self.M5_position = QtWidgets.QLCDNumber(self.centralwidget)
        self.M5_position.setGeometry(QtCore.QRect(800, 260, 64, 23))
        self.M5_position.setObjectName("M5_position")
        self.M5_position.setStyleSheet("background-color: rgb(0, 0, 0);")
        self.M12_position = QtWidgets.QLCDNumber(self.centralwidget)
        self.M12_position.setGeometry(QtCore.QRect(800, 580, 64, 23))
        self.M12_position.setObjectName("M12_position")
        self.M12_position.setStyleSheet("background-color: rgb(0, 0, 0);")
        self.M11_position = QtWidgets.QLCDNumber(self.centralwidget)
        self.M11_position.setGeometry(QtCore.QRect(800, 540, 64, 23))
        self.M11_position.setObjectName("M11_position")
        self.M11_position.setStyleSheet("background-color: rgb(0, 0, 0);")
        self.M6_position = QtWidgets.QLCDNumber(self.centralwidget)
        self.M6_position.setGeometry(QtCore.QRect(800, 300, 64, 23))
        self.M6_position.setObjectName("M6_position")
        self.M6_position.setStyleSheet("background-color: rgb(0, 0, 0);")
        self.M8_position = QtWidgets.QLCDNumber(self.centralwidget)
        self.M8_position.setGeometry(QtCore.QRect(800, 400, 64, 23))
        self.M8_position.setObjectName("M8_position")
        self.M8_position.setStyleSheet("background-color: rgb(0, 0, 0);")
        self.M9_position = QtWidgets.QLCDNumber(self.centralwidget)
        self.M9_position.setGeometry(QtCore.QRect(800, 440, 64, 23))
        self.M9_position.setObjectName("M9_position")
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

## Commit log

2021-02-01 urdf and gazebo folders
2021-02-01 rviz simulation setup done
    [quadrus.urdf]
2021-02-03 functionnal gazebo simulation
    [quadrus.urdf]
2021-02-03 grouped packages inside single folder
    [quadrus.urdf]
2021-02-10 added transmissions and controllers to all joints
2021-02-10 Contrôle des moteurs, test et méthodes
2021-02-16 parametrized urdf file using xacro
    [materials.xacro, quadrus.urdf, quadrus.xacro]
2021-02-17 Libre office calc du test dynamique couple moteur
    [Banc de test couple.ods]
2021-02-17 Déplacement des fichiers et modification de la fonction déplaceme fluide
2021-02-19 trajectory controller
    [quadrus.urdf, quadrus.xacro]
2021-02-19 realrobot yaml
    [quadrus_trajectory _RealRobot.yaml]
2021-02-19 changed simulation to qd_simulation
    [materials.xacro, quadrus.urdf, quadrus.xacro]
2021-02-19 changed quadrus_control to qd_control
    [qd_trajectory _RealRobot.yaml]
2021-02-20 Contrôle de plusieurs moteurs en même temps
2021-02-21 Changes to Motor Control
2021-02-21 Motor control ajustements
2021-02-22 Fixed motor's speed bug. Simplified joints limits check.
2021-02-22 Added missing packages
    Added four_wheel_steering_msgs, rosserial, urdf_geometry_parser
2021-02-23 hw interface + launch files
    [quadrus.urdf, quadrus.xacro]
2021-02-23 Identified motors
2021-02-23 Ajout de la fonction radToPulse et modif de la fonction angleToPulse
2021-02-23 Removed submodule urdf_geometry_parser
2021-02-23 rosserial integration
    [quadrus.xacro]
2021-02-23 Modified Arduino_Motors for Mechanical and Ros Compensation
2021-02-23 Ajout des fichiers CAD dans le git
    [2.54 mm DUPONT MALE PIN HEADER, IO, 2X20, RPi4ModelB.SLDPRT, 2.54 mm DUPONT MALE PIN HEADER, POE, 2X2, RPi4ModelB.SLDPRT, 2X USB2.0 PORTS, RPi4ModelB.SLDPRT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]
2021-02-23 Modified qd_control to completly control the first leg
    A action_server is still needed for the four legs
2021-02-24 4 leg trajectory
2021-02-26 Joint limits definition
2021-03-01 Updated urdf file
    [quadrus.xacro]
2021-03-10 fixed error in urdf file
    [quadrus.xacro]
2021-03-10 Change in MotorController's Header File
    Quadrus.h --> MotorController.h
2021-03-13 Added function motor_control for external loop
2021-03-17 angles csv
    [trunquated_data.csv]
2021-03-17 qd_control parameters
    [quadrus_backup.xacro, tuning.urdf]
2021-03-18 urdf test files
    [quadrus_forced.xacro, quadrus_nonzero.xacro]
2021-03-19 joint limits and hw interface
    [qd_joint_limits.yaml]
2021-03-19 hw interface debugging
    [qd_joint_limits.yaml]
2021-03-22 Added feedback and joint limits to hw inteface
2021-03-24 added platformIO folder for arduino
    [motor_benchmark.urdf, trunquated_data.ods, trunquated_data.xlsx]
2021-03-24 moved arduino control script to platformIO
2021-03-24 Ajustment low level motor control
2021-03-24 arduino code unitests and cleanup
2021-03-26 added feedback to arduino code
2021-03-27 split arduino code in multiple .cpp/.h
2021-03-27 Add files via upload
    Updated CAD parts and assemblies
    [Cylinde_bearing.SLDPRT, Embout_TPE_V3.SLDPRT, Femur.SLDASM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]
2021-03-27 added collisions and gravity to gazebo
    [quadrus.xacro, quadrus_backup.xacro, quadrus_forced.xacro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]
2021-03-27 removed motor_controller_h
2021-03-29 arduino configs
2021-03-29 benchmark controller tuning
    [motor_benchmark.xacro]
2021-03-31 Modified urdf collision volumes
    [motor_benchmark.xacro, quadrus.xacro]
2021-03-31 qd_trajectory for kinematics
2021-03-31 kinematics of spotmini
    [BACK.stl, BATTERY.stl, Back.stl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]
2021-04-01 integration of kinematics of spotmini
    [BACK.stl, BATTERY.stl, Back.stl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]
2021-04-01 Changed to load the right URDF file
2021-04-01 Changed the keywords for URDF in spot.py
2021-04-01 Fix main and kinematics merge issues
    Revert main to previous commit
2021-04-03 Changed ROS Launch to launch the kinematics node
2021-04-04 Updated URDF + added joint offsets for PYBullet
    [quadrus.urdf]
2021-04-07 added dummy link in urdf desc.
    [quadrus.xacro]
2021-04-07 Created final version of pyqt5 interface
    Missing few features
    [hardware.py]
2021-04-07 updated urdf file (body values)
    [quadrus.xacro]
2021-04-07 Added libraries for IMU
2021-04-08 Added IMU functionnalities for arduino
2021-04-08 Ajustments to low level control for 180 deg motor
2021-04-10 Final Update of the CAD Model
    [2.54 mm DUPONT MALE PIN HEADER, IO, 2X20, RPi4ModelB.SLDPRT, 2.54 mm DUPONT MALE PIN HEADER, POE, 2X2, RPi4ModelB.SLDPRT, 2X USB2.0 PORTS, RPi4ModelB.SLDPRT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]
2021-04-11 Mec compensations, joint limits, IMU commented
2021-04-11 Name update
    [Arduino-Mega.sldprt, Barre.sldprt, Bloc_bearing.SLDASM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]
2021-04-11 Code for motor setup before assembly
2021-04-11 Revert "Updated pyqt5 interface"
    This reverts commit ee32ba8492411ffab91564ac5ebec1809b84eab1.
    [hardware.py]
2021-04-14 control debugging
    [qd_joint_limits.yaml]
2021-04-14 Joint Limits update for qd_kinematics
2021-04-14 Updated joint limits in URDF for gazebo
    Joints are now revolute instead of continuous. Also added gazebo_msgs dependency in CMake of qd_simulation
    [quadrus.urdf, quadrus.xacro]
2021-04-14 kinematics tuning
2021-04-16 arduino code cleanup
2021-04-16 arduino code cleanup 2
2021-04-16 arduino code cleanup 3
2021-04-16 removed Arduino_moteurs
    [Banc de test couple.ods]

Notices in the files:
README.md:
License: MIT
